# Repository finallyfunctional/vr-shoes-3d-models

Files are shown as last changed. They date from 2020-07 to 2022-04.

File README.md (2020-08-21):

# 3D Design File for Virtual Reality Motorized Shoe

**Note: This is a work in progress**

The vr-shoe is a "shoe" or platform that straps to each of your feet. The shoes function like a treadmill where as you walk you stay i the same location. With a treadmill you can only walk forward and backward, but with the vr shoes you can turn, walk, and strafe in any direction.

The the vr shoes, along with a vr headset and saftey harness, are intended to be used while playing a vr game so that you can walk infintely in the game while staying in the same spot physically.

The design file is for [DesignSpark Mechanical](https://www.rs-online.com/designspark/mechanical-software).

I have three BOMs listed. BOM-Prototype-Dev-Pro is the BOM for the prototype/development version I'm working on now. In the future it could be a pro version. BOM-Consumer is the BOM for the version of the shoe that has cheaper components that might be more suitable for a consumer-level product. BOM-OnlyPoweredBraking is the BOM for a downgraded version of the shoe that only has powered braking and no powered walking assistance.

I'm currently working on the prototype version. Once I have a prototype working I will work on getting the cheaper (BOM-Consumer) version working. Then later I can try the powered braking version. I will also try out other versions of the shoes, such as a cheaper version that can only go forward/backwards (no strafing).

For more information, please visit [this page](http://evansalex.com/2020/08/04/a-motorized-shoe-to-be-used-with-virtual-reality-games-part-3/).

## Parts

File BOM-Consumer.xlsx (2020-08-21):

Item | Price | Quantity | Total | Percentage Total Cost | Link | Notes
623ZZ Bearing | 0.73 | 20 | 14.6 | 2.460107503 | https://www.bcprecision.com/collections/ball-bearings/products/623zz-3mm-x-10mm-x-4mm-shielded-deep-groove-precision-ball-bearings | Part of gearbox
R6-2RS Bearing | 0.75 | 30 | 22.5 | 3.791261563 | https://www.bcprecision.com/collections/ball-bearings/products/r6-2rs-8x22x7-sealed-greased-miniature-ball-bearings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 | Part of gearbox and axle supports
1623-2RS Bearings | 1.9 | 10 | 19 | 3.201509765 | https://www.bcprecision.com/collections/ball-bearings/products/1623-2rs-sealed-bearings-3-8-x-7-8-x-9-32-ball-bearings-pre-lubricated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 | Allow for shoe length adjustment
1/4 by 1.75 Hex Head Screws | 2.8 | 1 | 2.8 | 0.471801439 | https://www.mcmaster.com/92240A113 | Part of gearbox and axle supports
1/4 Hex Bar | 1.15 | 4 | 4.6 | 0.7751023641 | https://www.mcmaster.com/6512K121-6512K122 | Axles
Mending Bracket | 4.74 | 2 | 9.48 | 1.597384872 | https://www.mcmaster.com/1394A41 | Reinforcement for platform
6-32 by 0.5 Flat Head Screws and Nuts | 3.2 | 1 | 3.2 | 0.5392016446 | https://www.menards.com/main/hardware/fasteners-connectors/screws/sheet-metal-screws/grip-fast-reg-6-x-1-2-phillips-drive-zinc-flat-head-sheet-metal-screw-150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 | For screwing everything together
6-32 by 0.75 Flat Head Screws and Nuts | 3.2 | 1 | 3.2 | 0.5392016446 | https://www.menards.com/main/hardware/fasteners-connectors/screws/sheet-metal-screws/grip-fast-reg-6-x-3-4-phillips-drive-zinc-flat-head-sheet-metal-screw-120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 | For screwing everything together
6-32 by 1 Flat Head Screws and Nuts | 3.2 | 1 | 3.2 | 0.5392016446 | https://www.menards.com/main/hardware/fasteners-connectors/screws/sheet-metal-screws/grip-fast-reg-6-x-1-phillips-drive-zinc-flat-head-sheet-metal-screw-100-c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 | For screwing everything together
6-32 by 1.5 Flat Head Screws and Nuts | 3.2 | 1 | 3.2 | 0.5392016446 | https://www.menards.com/main/hardware/fasteners-connectors/screws/sheet-metal-screws/grip-fast-reg-6-x-1-1-2-phillips-drive-zinc-flat-head-sheet-metal-screw-7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 | For screwing everything together
3M, 30mm Screws | 5.74 | 1 | 5.74 | 0.9671929499 | https://www.mcmaster.com/91294A141/ | Axle for a few of the gears
Turnigy L3020B-600 Motor | 22.21 | 4 | 88.84 | 14.96958566 | https://hobbyking.com/en_us/turnigy-l3020b-600-brushless-motor-800w.html | Motors
Hobbyking X-Car 120A ESC | 25.15 | 4 | 100.6 | 16.9511517 | https://hobbyking.com/en_us/hobbykingr-x-car-120a-brushless-car-esc-sensored-sensorless.html | ESC for motors
ESP32 | 6.99 | 3 | 20.97 | 3.533455777 | https://usa.banggood.com/ESP32-Development-Board-WiFi+bluetooth-Ultra-Low-Power-Consumption-Dual-Cores-ESP-32-ESP-32S-Board-p-1109512.html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 | Controller board
Turnigy 2.2AH 3S 40C Battery | 16.41 | 2 | 32.82 | 5.530186867 | https://hobbyking.com/en_us/turnigy-2200mah-3s-40c-lipo-pack.html?queryID=81f73619b546928360c8537de74ae71a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 | Batteries
Hobbyking DC-4S Balance Charger | 10.62 | 1 | 10.62 | 1.789475458 | https://hobbyking.com/en_us/hobbykingr-dc-4s-balance-charger-cell-checker-30w-2s-4s.html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 | Battery charger
Safety Harness | 29.99 | 1 | 29.99 | 5.053330413 | https://www.amazon.com/Warthog-Universal-Harness-Pass-Thru-Buckles/dp/B074XHBCLD | Safety harness
Heavy Duty Swing Hanger | 16.59 | 1 | 16.59 | 2.795423526 | https://www.amazon.com/gp/product/B07QSSVBQ1/ref=ppx_yo_dt_b_asin_title_o00_s00?ie=UTF8&psc=1 | Hanger for safety harness
ABS filament | 8.94 | 2 | 17.88 | 3.012789189 | https://hobbyking.com/en_us/esun-3d-printer-filament-luminous-blue-3mm-abs-1kg-roll.html | ABS filament for parts
TPU filament | 14.28 | 1 | 14.28 | 2.406187339 | https://hobbyking.com/en_us/h-king-premium-pa-filament-500g-soft-flesh-pink.html | TPU filament for omni wheel rollers
TX60 Parallel Connector | 2.33 | 2 | 4.66 | 0.7852123949 | https://usa.banggood.com/XT60-Parallel-Adapter-Harness-Connector-Converter-p-938168.html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 | Connector for ESCs to battery
Accelerometers | 2.1 | 3 | 6.3 | 1.061553238 | https://usa.banggood.com/6DOF-MPU-6050-3-Axis-Gyro-With-Accelerometer-Sensor-Module-p-80862.html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 | Gyro to measure user position from harness and orientation of shoes
Rotacaster Omni Wheels | 9.9 | 16 | 158.4 | 26.69048141 | https://www.rotacasters.com/products/50mm-omnia-wheels/50mm-95a-durometer/ | Omni Wheels
Total |  |  | 593.47

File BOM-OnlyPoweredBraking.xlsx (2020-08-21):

Item | Price | Quantity | Total | Percentage Total Cost | Link | Notes
R6-2RS Bearing | 0.77 | 20 | 15.4 | 4.029198608 | https://www.bcprecision.com/collections/ball-bearings/products/r6-2rs-8x22x7-sealed-greased-miniature-ball-bearings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 | Part of gearbox and axle supports
1/4 by 1.75 Hex Head Screws | 2.8 | 1 | 2.8 | 0.7325815651 | https://www.mcmaster.com/92240A113 | Part of gearbox and axle supports
1/4 Hex Bar | 1.15 | 4 | 4.6 | 1.203526857 | https://www.mcmaster.com/6512K121-6512K122 | Axles
Mending Bracket | 4.74 | 2 | 9.48 | 2.48031187 | https://www.mcmaster.com/1394A41 | Reinforcement for platform
6-32 by 0.5 Flat Head Screws and Nuts | 3.2 | 1 | 3.2 | 0.8372360744 | https://www.menards.com/main/hardware/fasteners-connectors/screws/sheet-metal-screws/grip-fast-reg-6-x-1-2-phillips-drive-zinc-flat-head-sheet-metal-screw-150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 | For screwing everything together
6-32 by 0.75 Flat Head Screws and Nuts | 3.2 | 1 | 3.2 | 0.8372360744 | https://www.menards.com/main/hardware/fasteners-connectors/screws/sheet-metal-screws/grip-fast-reg-6-x-3-4-phillips-drive-zinc-flat-head-sheet-metal-screw-120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 | For screwing everything together
6-32 by 1 Flat Head Screws and Nuts | 3.2 | 1 | 3.2 | 0.8372360744 | https://www.menards.com/main/hardware/fasteners-connectors/screws/sheet-metal-screws/grip-fast-reg-6-x-1-phillips-drive-zinc-flat-head-sheet-metal-screw-100-c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 | For screwing everything together
6-32 by 1.5 Flat Head Screws and Nuts | 3.2 | 1 | 3.2 | 0.8372360744 | https://www.menards.com/main/hardware/fasteners-connectors/screws/sheet-metal-screws/grip-fast-reg-6-x-1-1-2-phillips-drive-zinc-flat-head-sheet-metal-screw-7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 | For screwing everything together
Turnigy D2205-2300KV Brushless Motor | 7.25 | 4 | 29 | 7.587451924 | https://hobbyking.com/en_us/brushless-motor-d2205-2300kv-cw.html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 | Motors
HobbyKing 10A ESC with Reverse | 13.41 | 4 | 53.64 | 14.0341697 | https://hobbyking.com/en_us/hobbykingr-tm-brushless-car-esc-10a-w-reverse.html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 | ESC for motors
ESP32 | 6.99 | 3 | 20.97 | 5.48651265 | https://usa.banggood.com/ESP32-Development-Board-WiFi+bluetooth-Ultra-Low-Power-Consumption-Dual-Cores-ESP-32-ESP-32S-Board-p-1109512.html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 | Controller board
Zippy Compact 1AH 3S 25C Lipo | 7.2 | 2 | 14.4 | 3.767562335 | https://hobbyking.com/en_us/zippy-compact-1000mah-3s-25c-lipo-pack.html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 | Batteries
Hobbyking DC-4S Balance Charger | 10.62 | 1 | 10.62 | 2.778577222 | https://hobbyking.com/en_us/hobbykingr-dc-4s-balance-charger-cell-checker-30w-2s-4s.html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 | Battery charger
Safety Harness | 29.99 | 1 | 29.99 | 7.846471835 | https://www.amazon.com/Warthog-Universal-Harness-Pass-Thru-Buckles/dp/B074XHBCLD | Safety harness
Heavy Duty Swing Hanger | 16.59 | 1 | 16.59 | 4.340545773 | https://www.amazon.com/gp/product/B07QSSVBQ1/ref=ppx_yo_dt_b_asin_title_o00_s00?ie=UTF8&psc=1 | Hanger for safety harness
ABS filament | 8.94 | 2 | 17.88 | 4.678056566 | https://hobbyking.com/en_us/esun-3d-printer-filament-luminous-blue-3mm-abs-1kg-roll.html | ABS filament for parts
TPU filament | 14.28 | 1 | 14.28 | 3.736165982 | https://hobbyking.com/en_us/h-king-premium-pa-filament-500g-soft-flesh-pink.html | TPU filament for omni wheel rollers
TX60 Parallel Connector | 2.33 | 2 | 4.66 | 1.219225033 | https://usa.banggood.com/XT60-Parallel-Adapter-Harness-Connector-Converter-p-938168.html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 | Connector for ESCs to battery
Accelerometers | 2.1 | 3 | 6.3 | 1.648308521 | https://usa.banggood.com/6DOF-MPU-6050-3-Axis-Gyro-With-Accelerometer-Sensor-Module-p-80862.html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 | Gyro to measure user position from harness and orientation of shoes
Rotacaster Omni Wheels | 9.9 | 12 | 118.8 | 31.08238926 | https://www.rotacasters.com/products/50mm-omnia-wheels/50mm-95a-durometer/ | Omni Wheels
Total |  |  | 382.21

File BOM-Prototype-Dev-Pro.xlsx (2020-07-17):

Item | Price | Quantity | Total | Percentage Total Cost | Link | Notes
623ZZ Bearing | 0.73 | 20 | 14.6 | 1.27588919 | https://www.bcprecision.com/collections/ball-bearings/products/623zz-3mm-x-10mm-x-4mm-shielded-deep-groove-precision-ball-bearings | Part of gearbox
R6-2RS Bearing | 0.75 | 30 | 22.5 | 1.966267587 | https://www.bcprecision.com/collections/ball-bearings/products/r6-2rs-8x22x7-sealed-greased-miniature-ball-bearings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 | Part of gearbox
1623-2RS Bearings | 1.9 | 10 | 19 | 1.66040374 | https://www.bcprecision.com/collections/ball-bearings/products/1623-2rs-sealed-bearings-3-8-x-7-8-x-9-32-ball-bearings-pre-lubricated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 | Allow for shoe length adjustment
1/4 by 1.75 Hex Head Screws | 2.8 | 1 | 2.8 | 0.2446910775 | https://www.mcmaster.com/92240A113 | Part of gearbox and axle supports
1/4 Hex Bar | 1.15 | 4 | 4.6 | 0.4019924845 | https://www.mcmaster.com/6512K121-6512K122 | Axles
Mending Bracket | 4.74 | 2 | 9.48 | 0.8284540767 | https://www.mcmaster.com/1394A41 | Reinforcement for platform
6-32 by 0.5 Flat Head Screws and Nuts | 3.2 | 1 | 3.2 | 0.2796469457 | https://www.menards.com/main/hardware/fasteners-connectors/screws/sheet-metal-screws/grip-fast-reg-6-x-1-2-phillips-drive-zinc-flat-head-sheet-metal-screw-150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 | For screwing everything together
6-32 by 0.75 Flat Head Screws and Nuts | 3.2 | 1 | 3.2 | 0.2796469457 | https://www.menards.com/main/hardware/fasteners-connectors/screws/sheet-metal-screws/grip-fast-reg-6-x-3-4-phillips-drive-zinc-flat-head-sheet-metal-screw-120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 | For screwing everything together
6-32 by 1 Flat Head Screws and Nuts | 3.2 | 1 | 3.2 | 0.2796469457 | https://www.menards.com/main/hardware/fasteners-connectors/screws/sheet-metal-screws/grip-fast-reg-6-x-1-phillips-drive-zinc-flat-head-sheet-metal-screw-100-c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 | For screwing everything together
6-32 by 1.5 Flat Head Screws and Nuts | 3.2 | 1 | 3.2 | 0.2796469457 | https://www.menards.com/main/hardware/fasteners-connectors/screws/sheet-metal-screws/grip-fast-reg-6-x-1-1-2-phillips-drive-zinc-flat-head-sheet-metal-screw-7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 | For screwing everything together
3M, 30mm Screws | 5.74 | 1 | 5.74 | 0.5016167089 | https://www.mcmaster.com/91294A141/ | Axle for a few of the gears
Flipsky 5065 270kv motor | 50.91 | 4 | 203.64 | 17.79603251 | https://www.banggood.com/Flipsky-5065-270KV-1550W-Brushless-Sensored-Motor-Shaft-8mm-for-Electric-Skateboard-Rc-Model-p-1333994.html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 | Motors
Flipsky Mini VESC | 57.34 | 4 | 229.36 | 20.04369484 | https://www.banggood.com/Flipsky-Mini-FSESC4_20-50A-ESC-Based-Upon-VESC-With-Aluminum-Anodized-Heat-Sink-for-Rc-Car-p-1349277.html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 | ESC for motors
Arduino Uno Wifi Rev2 | 44.8 | 3 | 134.4 | 11.74517172 | https://store.arduino.cc/usa/arduino-uno-wifi-rev2 | Controller board
4mm bullet connectors | 5.08 | 1 | 5.08 | 0.4439395263 | https://www.banggood.com/10-Pair-4mm-Gold-Bullet-Connector-Banana-Plug-For-ESC-Battery-Motor-p-1010239.html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 | Connectors for VESC
Turnigy 5AH 3S 60C Lipo | 45.08 | 2 | 90.16 | 7.879052696 | https://hobbyking.com/en_us/turnigy-heavy-duty-5000mah-3s-60c-lipo-pack-w-xt-90.html | Batteries
Hobbyking DC-4S Balance Charger | 10.62 | 1 | 10.62 | 0.9280783011 | https://hobbyking.com/en_us/hobbykingr-dc-4s-balance-charger-cell-checker-30w-2s-4s.html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 | Battery charger
Safety Harness | 29.99 | 1 | 29.99 | 2.62081622 | https://www.amazon.com/Warthog-Universal-Harness-Pass-Thru-Buckles/dp/B074XHBCLD | Safety harness
Heavy Duty Swing Hanger | 16.59 | 1 | 16.59 | 1.449794634 | https://www.amazon.com/gp/product/B07QSSVBQ1/ref=ppx_yo_dt_b_asin_title_o00_s00?ie=UTF8&psc=1 | Hanger for safety harness
PETG filament | 28.99 | 3 | 86.97 | 7.600279647 | https://coexllc.com/product/3d-filaments/petg-filament/petg/black-petg-175mm-1kg/ | PETG filament for parts
TPU filament | 29.99 | 1 | 29.99 | 2.62081622 | https://www.amazon.com/gp/product/B00TI3JUTM/ref=ppx_yo_dt_b_asin_title_o03_s00?ie=UTF8&psc=1 | TPU filament for omni wheel rollers
Dual ESC TX90 Parallel Connector | 8.99 | 2 | 17.98 | 1.571266276 | https://diyelectricskateboard.com/products/dual-esc-xt90-parallel-connector | Connectors for VESCs to battery
Rotacaster Omni Wheels | 9.9 | 20 | 198 | 17.30315477 | https://www.rotacasters.com/products/50mm-omnia-wheels/50mm-95a-durometer/ | Omni Wheels
Total |  |  | 1144.3

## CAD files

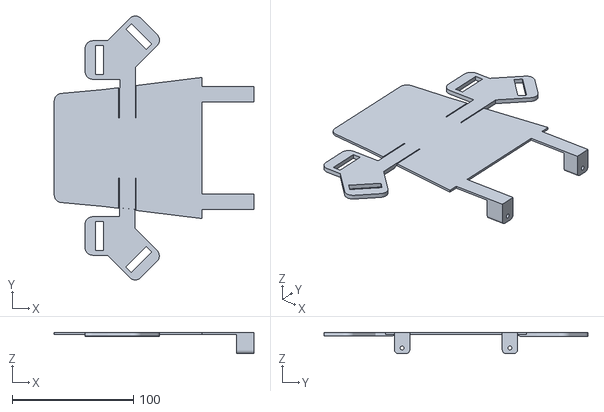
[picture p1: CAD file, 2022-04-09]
passive-vr-shoe/stl/v1/shorter foot strap - row 29.stl
164.6 x 217.7 x 17.5

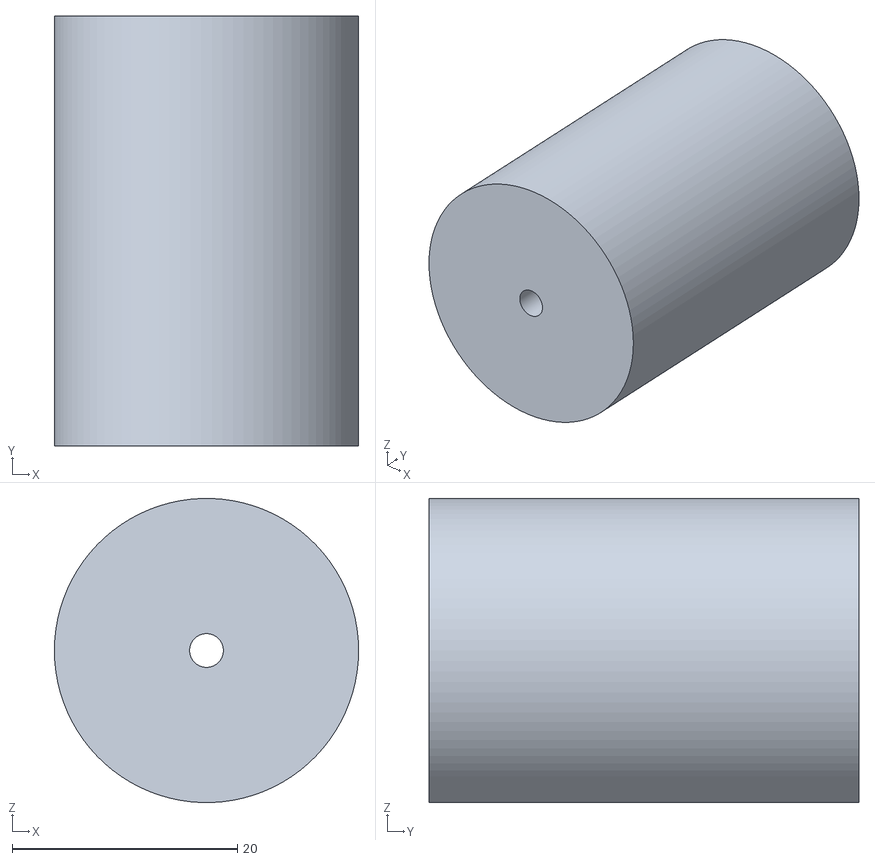
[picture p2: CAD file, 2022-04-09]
passive-vr-shoe/stl/v1/wheel - row 11.stl
27.0 x 38.2 x 27.0

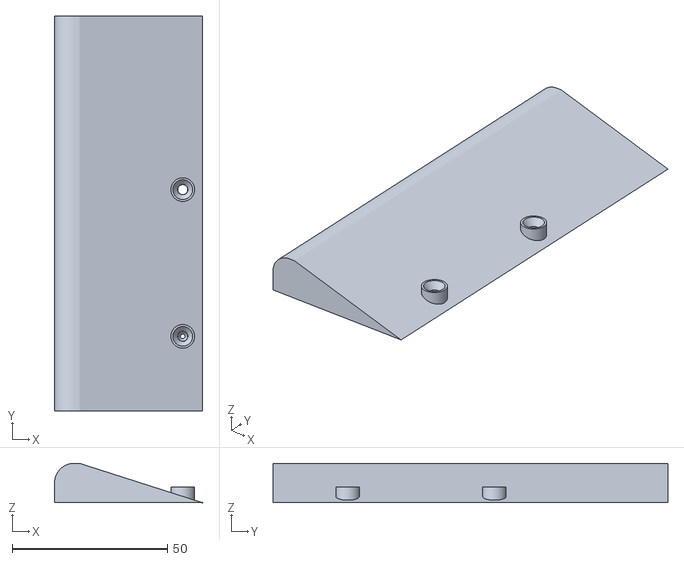
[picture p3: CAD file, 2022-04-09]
passive-vr-shoe/stl/v1/front toes spacer - row 4.stl
47.6 x 127.0 x 12.7

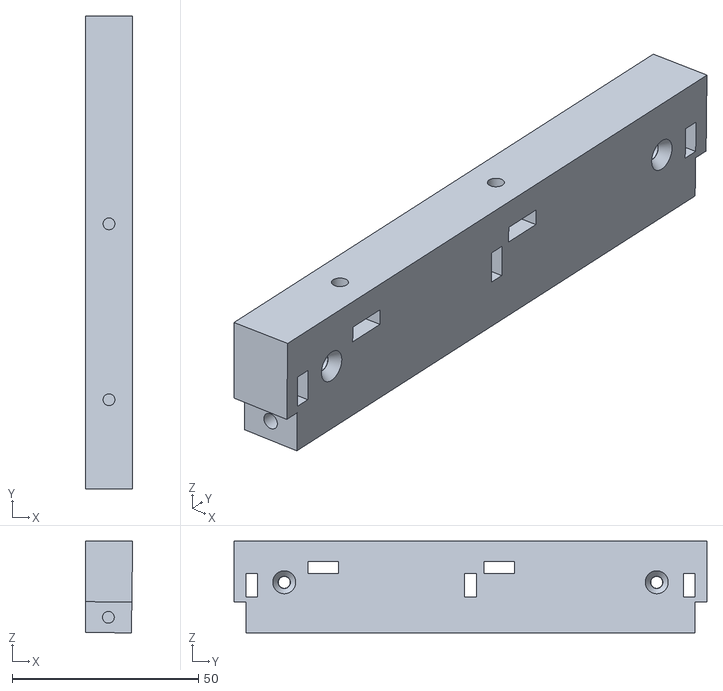
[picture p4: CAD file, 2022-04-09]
passive-vr-shoe/stl/v1/top front stopper - row 3.stl
12.7 x 127.0 x 24.7

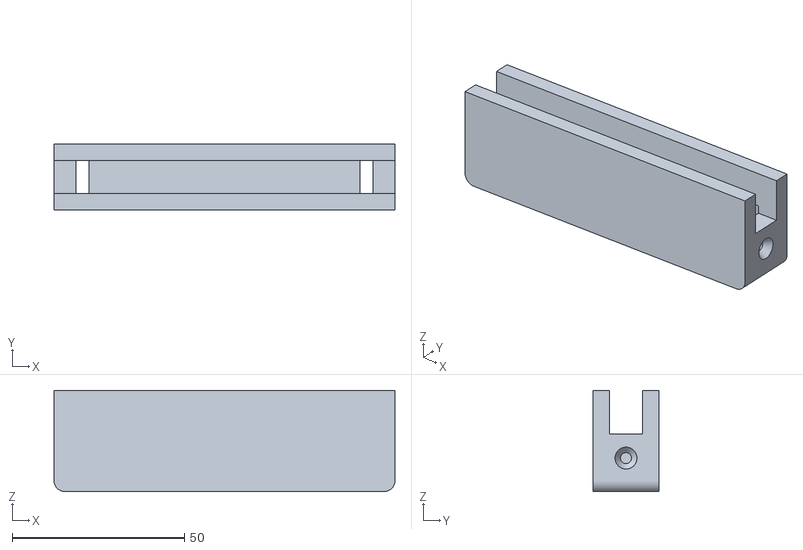
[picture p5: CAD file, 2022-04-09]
passive-vr-shoe/stl/v1/friction piece - row 24.stl
99.1 x 19.1 x 29.4

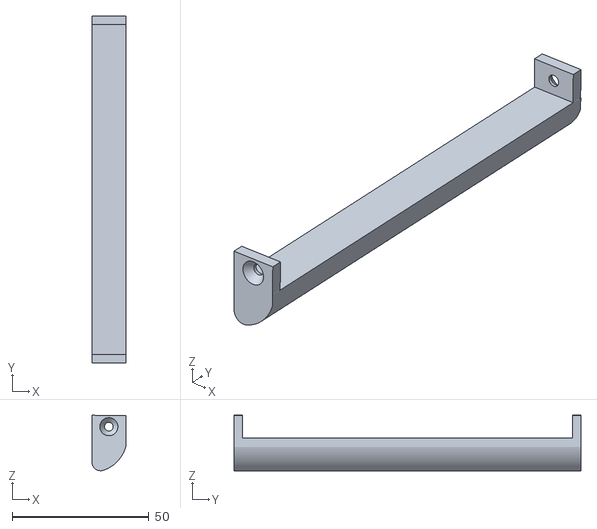
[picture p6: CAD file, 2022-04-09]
passive-vr-shoe/stl/v1/front stopper long bottom - row 7.stl
12.5 x 127.0 x 20.3

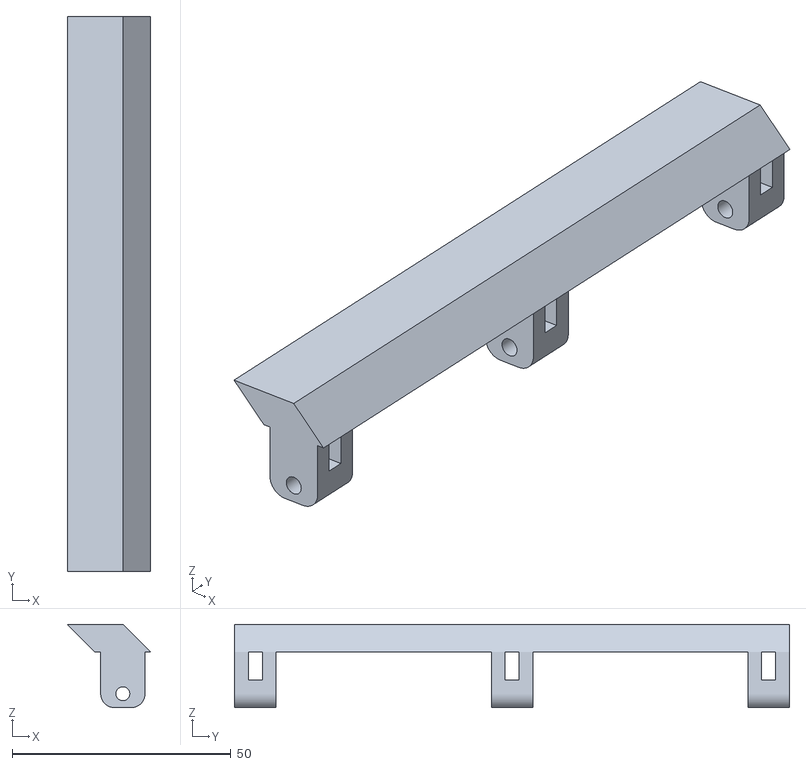
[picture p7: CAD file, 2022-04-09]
passive-vr-shoe/stl/v1/shorter middle-back - row 22.stl
19.0 x 127.0 x 19.0

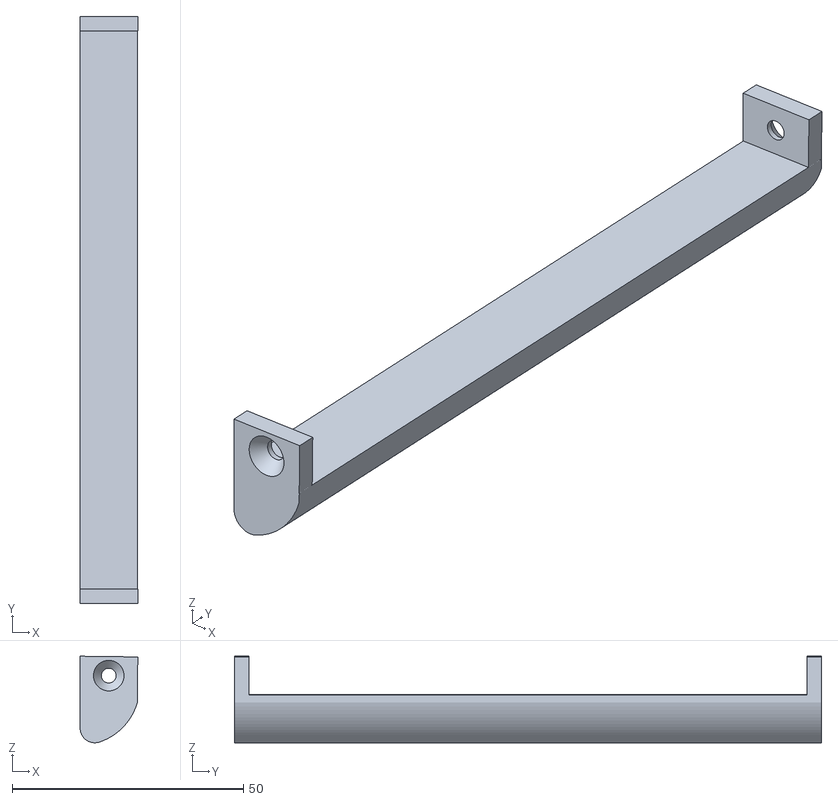
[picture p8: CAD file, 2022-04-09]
passive-vr-shoe/stl/v1/front stopper medium bottom - row 6.stl
12.5 x 127.0 x 18.7

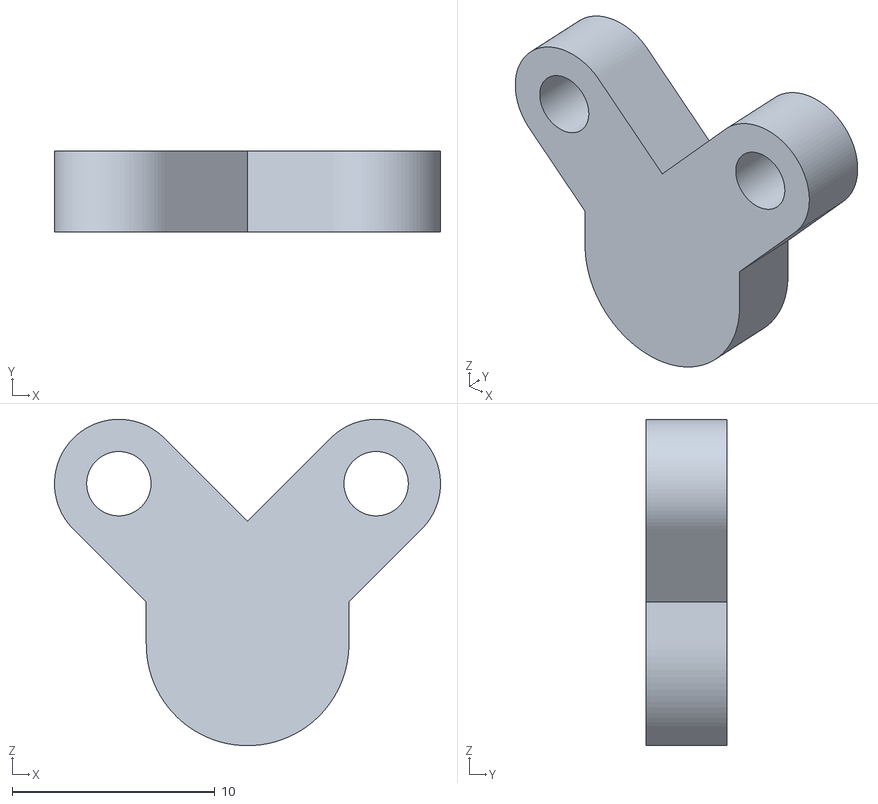
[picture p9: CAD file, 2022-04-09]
passive-vr-shoe/stl/v1/axle end cover - row 8.stl
19.0 x 4.01 x 16.1

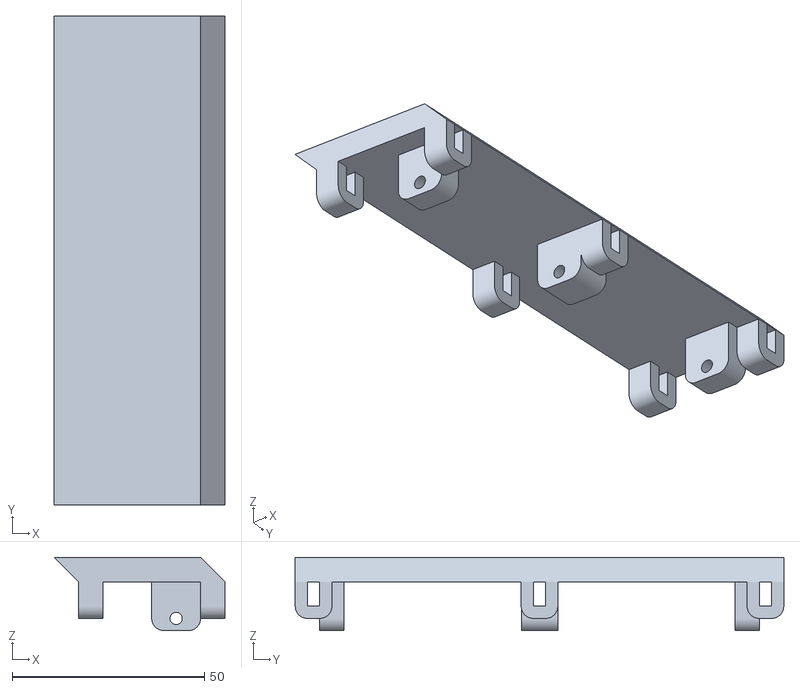
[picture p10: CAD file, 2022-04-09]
passive-vr-shoe/stl/v1/middle-back - row 21.stl
44.5 x 127.0 x 19.0

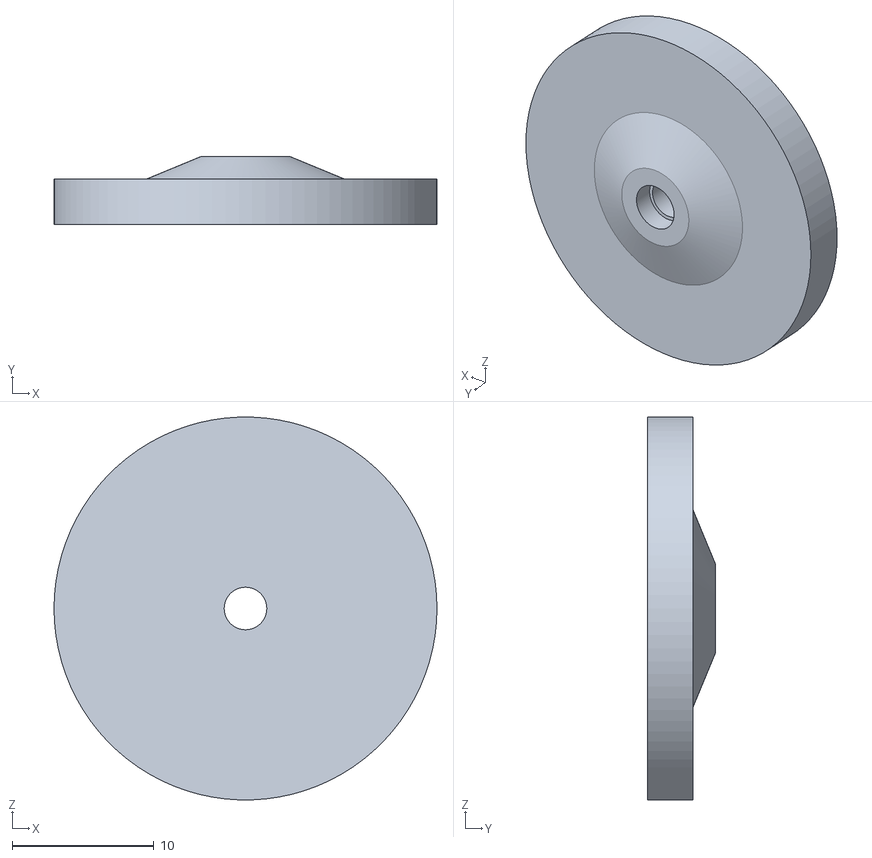
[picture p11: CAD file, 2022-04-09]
passive-vr-shoe/stl/v1/wheel end - row 12.stl
27.0 x 4.76 x 27.0

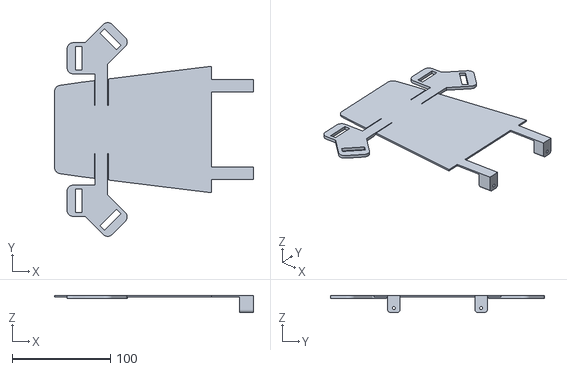
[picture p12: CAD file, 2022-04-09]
passive-vr-shoe/stl/v1/longer foot strap - row 30.stl
202.7 x 217.7 x 17.5

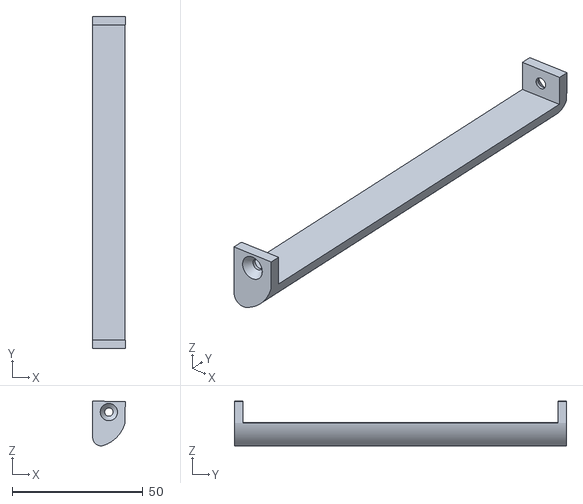
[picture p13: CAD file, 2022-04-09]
passive-vr-shoe/stl/v1/front stopper short bottom - row 5.stl
12.5 x 127.0 x 17.1

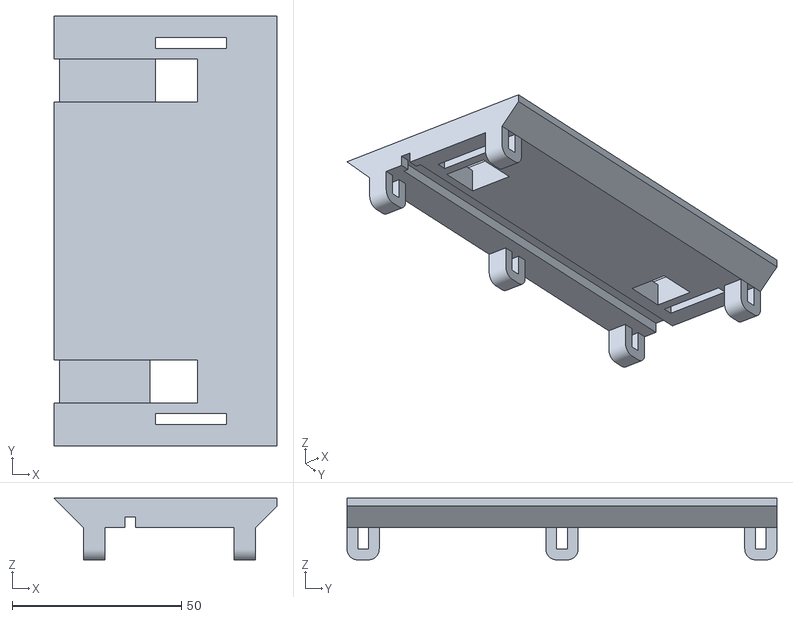
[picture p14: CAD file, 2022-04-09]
passive-vr-shoe/stl/v1/middle-front - row 20.stl
65.9 x 127.0 x 18.2

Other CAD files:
passive-vr-shoe/stl/v1/wheel spacer - row 13.stl
passive-vr-shoe/stl/v1/front - row 2.stl
passive-vr-shoe/stl/v1/back - row 18.stl
passive-vr-shoe/stl/v1/foot strap - row 28.stl
passive-vr-shoe/stl/v1/back stopper top - row 19.stl
passive-vr-shoe/stl/v1/longer middle-back - row 23.stl
safety-structure/Ceiling-Mounted-Support-Rig/v1/stl/0.5in conduit guide - row 38.stl
safety-structure/Ceiling-Mounted-Support-Rig/v1/stl/0.75in conduit guide - row 36.stl
safety-structure/Ceiling-Mounted-Support-Rig/v1/stl/0.75in conduit top nuts cap - row 37.stl
safety-structure/Ceiling-Mounted-Support-Rig/v1/stl/0.875 lock nut cover - row 14.stl
safety-structure/Ceiling-Mounted-Support-Rig/v1/stl/bottom slider - row 39.stl
safety-structure/Ceiling-Mounted-Support-Rig/v1/stl/brace square spacer - row 15.stl
safety-structure/Ceiling-Mounted-Support-Rig/v1/stl/bungee clamp - row 48.stl
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

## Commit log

2020-04-26 Initial commit. Added gitignore and current design file.
2020-04-26 Updated y direction supports with a hole to make it easy to insert the rod for the idler support.
2020-04-30 Updated platform so it's 3D printable on a Prusa i3.
2020-05-02 Updated y gearbox frame 3 with 2 holes on the side.
2020-05-03 Made some tweaks. Added hex holes to sink nuts into. Redid the spacers for tensioning the chain.
2020-05-24 Added electronics. Spaced everything out. Added gearbox covers.
2020-05-25 Added screw holes to hold everything together.
2020-05-26 Made some modifications to the omni wheel to make it easier to print. Added BOMs.
    [BOM-High.xlsx, BOM-Low.xlsx]
2020-06-04 Added bridges to several parts to make them easier to 3d print.
2020-06-13 Added bracing on both sides of gears in gearbox.
2020-06-14 Redesigned omni wheels to have bearings in the arms instead of the rollers. The rollers can be secured better.
2020-06-15 Redesigned omni wheel to securely hold the bearings and rollers in place.
2020-06-16 Updated omni wheels to be much stronger. These should never break. However, they are much wider than previously. It'll be hard to fit everything under a 8"x7" platform now.
2020-06-17 Modeled another omni wheel design. This one ended up being wide too.
2020-06-19 Redesigned forward and sideways drives so that the larger omni wheels will fit.
2020-06-19 Finished the redesign for the larger omni wheels.
2020-06-27 Forgot a few holes.
2020-06-28 Reverted changes back to the version I had when I used 2 inch wheels. Updated design to work with 50mm Rotacaster omni wheels. Moved sideways drive towards the back of the shoe so that it will be eas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
2020-07-02 Added leg coupler and binding.
2020-07-08 Added holes to platform to screw everything together.
2020-07-08 Added cutouts in platform for motors and gears.
2020-07-12 Updated X beam on leg coupler to be easier to print. Updated rods top so the middle of the X beam can slide past it.
2020-07-12 Made electronics box longer so that wire management is easier.
2020-07-12 Added channels for wires.Modified leg coupler parts so I can use 0.5in screws for securing parts to the rods.
2020-07-14 Added supports for wire channels.
2020-07-17 Redid straps on the binding.
2020-07-17 Renamed BOMs.
    [BOM-OnlyPoweredBraking.xlsx, BOM-PoweredWalking.xlsx, BOM-Prototype.xlsx]
2020-07-17 Updated BOMs.
    [BOM-OnlyPoweredBraking.xlsx, BOM-PoweredWalking.xlsx, BOM-Prototype.xlsx]
2020-07-17 Made wire channels easier to work with.
2020-08-08 Made shoe thinner by 0.5 inches. Added cover over top of platform. Integrated buttons that go on the top of the platform. Redid electronics box to fit the new electronics. Added a cover over the batt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
2020-08-09 Added slots or holes for nuts to every spot that a screw is used.
2020-08-09 Added slits for nuts to corner axle support.
2020-08-21 Made several updates to the shoe to make it easier to assemble.
    [BOM-Consumer.xlsx, BOM-OnlyPoweredBraking.xlsx, BOM-PoweredWalking.xlsx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]
2020-11-15 Completed all the modeling before starting printing. Added all the rest of the screw holes, spots for the hall sensors, etc.
2020-11-15 Cut binding in half so it can actually fit on my printers.
2020-12-06 Various updates. Mostly to the electronic box to make the wire management better and cover easier to put on.
2021-01-26 Made a motorized, forward/back only VR shoe.
2021-02-07 Added a way to screw the side cover into place.
2021-10-11 Added ceiling mounted support rig I built.
2022-02-03 Uploaded latest model file for the ceiling mounted support rig.
2022-04-03 Made some small modifications while creating the hackaday.io guide. Mostly just adding bolts.
2022-04-03 Added harness couplers fo 0.75in conduit.
2022-04-03 Added harness coupler pieces for conduit.
2022-04-03 Added all the stls for the ceiling mounted rig 3D printed parts.
    [0.5in conduit guide - row 38.stl, 0.75in conduit guide - row 36.stl, 0.75in conduit top nuts cap - row 37.stl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]
2022-04-09 Added 3D model files for passive VR shoe.
    [axle end cover - row 8.stl, back - row 18.stl, back stopper top - row 19.stl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]
2022-05-29 Added v2 design for passive vr shoe.
    [axle end cover - row 8.stl, back - row 18.stl, back stopper top - row 19.stl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]
2022-10-18 Added first draft of leg mechanism, v1-3 for the linkage assembly device, and the design for my new ceiling mounted rig.
    [0.5in conduit guide - row 38.stl, 0.75in conduit guide - row 36.stl, 0.75in conduit top nuts cap - row 37.stl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]
2023-03-26 Added v3 for passive VR shoe and v2 for ceiling mounted support rig
